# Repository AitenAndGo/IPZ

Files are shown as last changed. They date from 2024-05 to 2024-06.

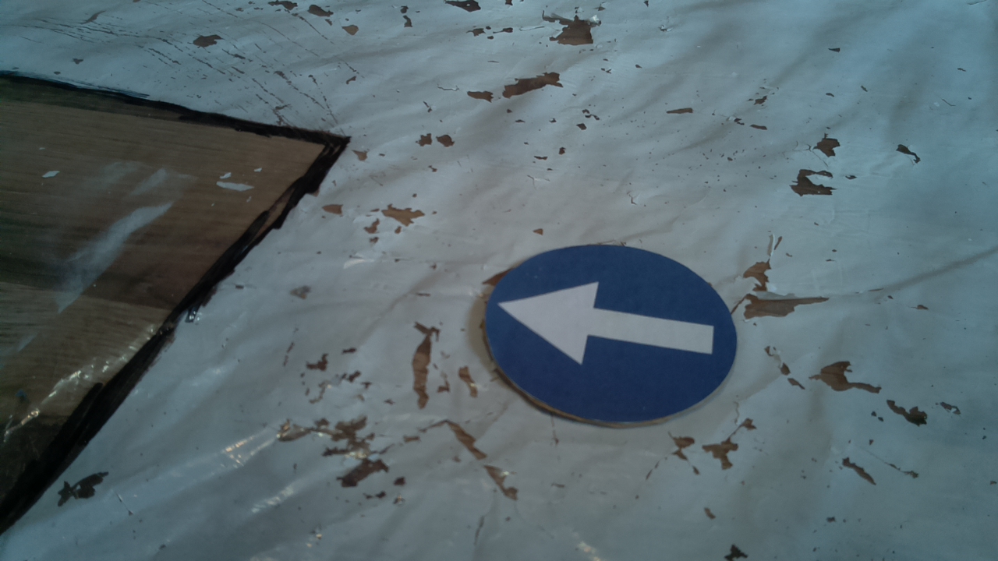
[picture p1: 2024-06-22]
Car/VisionSystem/photos/test/img104.jpg

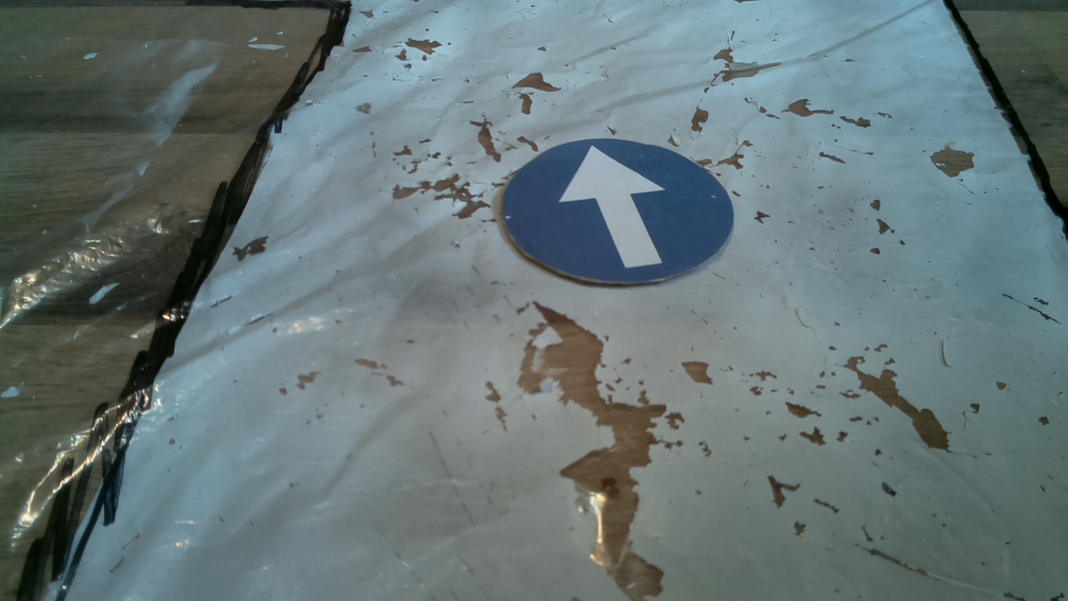
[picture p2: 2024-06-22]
Car/VisionSystem/photos/test/img115.jpg

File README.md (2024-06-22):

# PROJEKT AUTONOMICZENGO SAMOCHODU:
[kliknij aby obejrzeć](url_do_filmu)

# Projekt autonomicznego samochodu 

Celem projektu będzie stworzenie autonomicznego modelu samochodu potrafiącego poruszać się po makiecie miasta ze skrzyżowaniem i światłami, samochód będzie w stanie sam poruszać się po drodze, odpowiednio reagować na światła drogowe, oraz podejmować decyzje o swojej trasie.

___
## 1. Wprowadzenie
W ramach kursu *Interdyscyplinarny projekt zespołowy* przez 15 tygodni w grupie 4 osób będziemy pracować nad stworzeniem automocznego pojazdu, potrafiącego poruszać się na stworzonej drodze i reagować na światła drogowe. Cały projekt jest udokumentowany a pliki będą dostępne [tutaj](https://github.com/AitenAndGo/IPZ "tutaj!"). Rownież poniżej będzie dostępny i pokazany cały proces tworzenia projektu, więc chętne osoby będą mogły spróbować odtworzyć tą koncepcję. Samo stowrzenie takiego pojazdu wraz z całym systemem i makietą jest zadaniem wymagającym dużej wiedzy z zakresu programowania, elektroniki i mechaniki. Do dzieła!

## 2. Cele projektu
+ zbudowanie pojazdu mobilnego
+ stworzenie środowiska po którym będzie poruszał się pojazd
+ stowrzenie systemu świateł drogowych na skrzyżowaniu
+ implementacja oprogramowania z systemem wizyjnym
+ stworzenie bazy danych
+ stworzenie strony internetowej

## 3. Plan projektu
Szczegółowy plan projektu dostępny jest [tutaj](https://github.com/AitenAndGo/IPZ/blob/main/Documentation/Plan.txt "tutaj!")

___
# Realizacja
Realizacja projektu skłądała się na 4 główne etapy:
+ Makieta skrzyżowania
+ Strona internetowa
+ Program strujący makietą miasta
+ samochód
Wszystkie potrzebne kody i modele znajdują się na [tutaj](https://github.com/AitenAndGo/IPZ "tutaj!"). Teraz opiszę każdy z etapów, aby przybliżyć sposób w jaki projekt został zrealizowany.
Zaczynajmy!

##  Makieta
Makieta miała składać się ze skrzyżowania, które posiada 4 drogi wejściowe i wszystkie z dróg łączą się ze sobą tworząc zewnętrzy prostokątny pierścień. Na skrzyżowaniu są 4 światła drogowe, każde z nich osobne do kierowania ruchem przy danej drodze wejściowej. przed wjazdem na środek skrzyżowania na każdej z dróg jest również ustawiony czytnik RFID. Czytnik ten za każdym razem, gdy przejeżdza auto ze swoją kartą RFID zczytuje ją i informuje server o tym że dane auto znalazło się właśnie na danej drodze. Aby wszystko mogło działać potrzebny był mikrokontroler do sterowania światłąmi i RFID. Wybraliśmy esp32, które posiada modół bluetooth oraz wifi co ułatwi komunikację z samochodem. Wszystkie światła i czujniki trzebabyło połączyć z mikrokontrolerem co nie jest lada zadaniem. Ze względu na wielkość makiety i ilość potrzebnych połączeń (tutaj warto dodać że czujniki RFID było zkomunikowane za pomocą protokołu SPI), wykorzystaliśmy płytkę prototypową do dzięki której uzyskaliśmy uporządkowany i zchludny układ elektryczny makiety.
Poniżej pewne zdjęcia i filmy przedstawiające proces powstawania makiety:
makieta
435650640_2062892654094104_2510210449119449921_n
440818486_815108286667908_91705931173108030_n


## Program sterujący makietą
Makieta zwana przez nas "miastem" pełni w tym projekcie wiele aspektów. Odpowiada ona za odpowiednie przełączanie świateł, komunikuje się z serverem i przesyła informacje o odczytanych przejazdach samochodu, oraz musi komunikować się z samochodem aby informować go w momencie gdy przejeżdża on przez skrzyżowanie czy aktualne światło mu na to zezwala. Wszelkie kody można znaleźć w katalogu projektu i powinny one wyjaśnić wszelkie niepewności.

## Strona internetowa
Projekt miał być tak zrobiony, że w teorii można by było wiele samochodów puścić po podobnej makiecie, tylko większej. W związku z tym na serwerze python-anywhere postawiono bardzo prostą stronę internetową (Flask + HTML) oraz podłączono do niej relacyjną bazę danych (MySQL). Baza ta ma 3 tabele: Car, Server oraz City_Trafic. W pierwszej tabeli są wszystkie samochody, które mogą jeździć po makiecie - każdy ma swoje ID oraz status isDriving (czy aktualnie ejst w trakcie jazdy). Dodatkowo przy każdy są przyciski START i STOP - samochody maja być autonomiczne i można nimi sterowac z poziomu strony internetowej, klikając w przycisk Start samochód o danym ID startuje. Druga tabela Server przechowuje informacje o tym, o której godzinie zaczął i skończył jazdę samochód o danym ID w mieście o danym ID. Trzecia tabela to jest kontrola, o której godzinie samochód o danym ID przejechał przez światła (w naszym projekcie były 4: Północ, Południe, Wschód i Zachód).





## Samochód
Na samochód składają się w sumie 4 części:
+ model 3D
+ elektronika
+ model do rozpoznawania znaków
+ program sterujący
Pliki .stl do wydrukowania modelu samochodu można znaleźć w repozytrium projektu. Składa się z dwóch warst, pomiędze znajduje się powerbank, który głównie determinuje wymiary samochodu. Zawera specjalny uchwyt na kamerę a sterowanie kołami przednimi odbywa się przy pomocy micro-serva. W kontekście elektroniki samochód jest napędzany dwoma silnikami na tylnej osi. Silniki są kontrolowane sygnałąmi PWM z drivera LN289. Zasilanie silników jest z pakietu Li-Po 3s i przetwornicy zmniejszającej napięcie do 6V. Głównym komponentem jest RaspberryPi 4 które pełni funkcję sterowania całym samochodem. Złożony samohchód wygląda następująco:

Do rozpoznawania znaków użyto biblioteki fastAi, która kożysta z PyTorch. Zostało zrobione łącznie 400 zdjęć o 4 różnych etykietach tj. prawo, lewo, prosto i bez znaku. Następnie wytrenowano model zgodnie z kodem dostępnym w repozytorium projektu. Całość została wykonany w google colab więc w łatwy sposób można prześledzić tok postępowania. Gotowy model posiadał błąd w wysokości 1%.
Najtrudniejszym zadaniem było stworzenie programu do sterowania. Aby przygotować program jeszcze przed stworzeniem samochodu i dostępem do mikrokomputera została stworzona symulacja w środowisu Unity. Symulacja pozwalała na przygotowanie podstaw skryptu. Działanie skryptu i symulacji przedstawia poniższe nagranie:
### SIMULATION VIDEO:
[kliknij aby obejrzeć](https://github.com/AitenAndGo/IPZ/assets/87769038/a0adc0f1-8832-4500-9a60-e44e0641514c "tutaj!")

Następnie gdy samochód był gotowy należało przygotować środowisko na raspberry. W celu instalacji wszystkich bibliotek zaleca się skorzystanie z minicondy i następnie na stworzonym wirtualnym środowisku zainstalować wszystkie wszystkie biblioteki. Ważne jest również aby system był odpowiedi do zainstalowania PyTorch (potrzebny system 64-bitowy). Program składa się z lokalnej strony na której można mieć podgląd na żywo z widoku kamery co jest bardzo pomocne do debugowania błędów. 
### REMOTLY CONTROLLED CAMERA TEST

[kliknij aby obejrzeć](https://github.com/AitenAndGo/IPZ/assets/87769038/37e9659a-60ab-4ea5-bf75-93e4743b6fed "tutaj!")

Gdy wszystko było przygotowane możnabyło przetestować kod na stowrzonym testowtm torze. Po wielu próbach osiągnięto pozytywne rezultaly co prezentuje poniższy film:

[kliknij aby obejrzeć](https://github.com/AitenAndGo/IPZ/assets/87769038/8e6763ad-770e-4cb4-8f08-51653d83972e "tutaj!")

Całość już połączonego systmu wszytskich elementó można zobaczyć na głównym filmie przedstawiającym cały projekt!.

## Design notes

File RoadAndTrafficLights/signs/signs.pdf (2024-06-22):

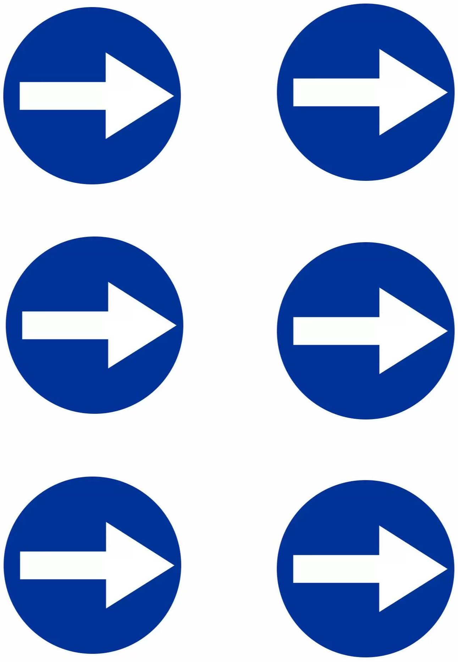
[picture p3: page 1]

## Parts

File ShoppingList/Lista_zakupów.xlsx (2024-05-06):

Nazwa: | Ilość: | Cena/1szt.: | Cena całkowita: | Link:
silnik z kołem (mamy 2, potrzebujemy 2) | 4 | 7 | 28 | https://botland.com.pl/silniki-dc-katowe-z-przekladnia/3696-kolo-silnik-65x26mm-5v-z-przekladnia-48-1-5903351248129.html
Serwo do kół przednich | 1 | 23 | 23 | https://botland.com.pl/serwa-typu-micro/20435-serwo-mg-90s-micro-180-stopni-metalowa-przekladnia-5904422380915.html
Driver do silników | 1 | 19 | 19 | https://botland.com.pl/arduino-shield-kontrolery-silnikow-i-serw/8224-l293d-motor-driver-board-sterownik-silnikow-16v06a-nakladka-dla-arduino-iduino-st1138-59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
goldpin | 1 | 10 | 10 | https://botland.com.pl/gniazda-szpilkowe-goldpin/9499-zestaw-zlacz-dla-esp32-thing-2x-1x20-raster-254mm-sparkfun-prt-14311-5904422313494.html
Płytka drukowana | 1 | 10 | 10 | https://botland.com.pl/plytki-uniwersalne/20269-plytka-drukowana-uniwersalna-dwustronna-90x150mm-5904422380533.html
Czujniki RfiD | 4 | 15 | 60 | https://botland.com.pl/moduly-i-tagi-rfid/6765-modul-rfid-mf-rc522-1356mhz-spi-karta-i-brelok-5904422335014.html
bateria lipo do silników | 1 | 36 | 36 | https://botland.com.pl/akumulatory-li-pol-3s-111v-/1307-pakiet-li-pol-redox-700mah-20c-3s-111v-5903754000454.html
ESP | 1 | 50 | 50 | https://botland.com.pl/moduly-wifi-i-bt-esp32/8893-esp32-wifi-bt-42-platforma-z-modulem-esp-wroom-32-zgodny-z-esp32-devkit-5904422337438.html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
śrubki i nakrętki (zestaw) | 1 | 11.9 | 11.9 | https://botland.com.pl/srubki-i-nakretki/637-zestaw-srubek-podkladek-i-nakretek-330szt-5410329304478.html
 |  |  | 247.9

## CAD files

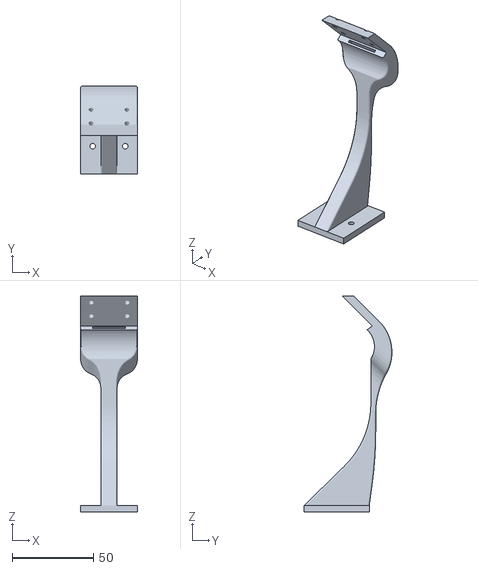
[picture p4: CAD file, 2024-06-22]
Car/mechanics/car/stlFiles/kamera_uchwyt_3.stl
35.0 x 53.9 x 132.5

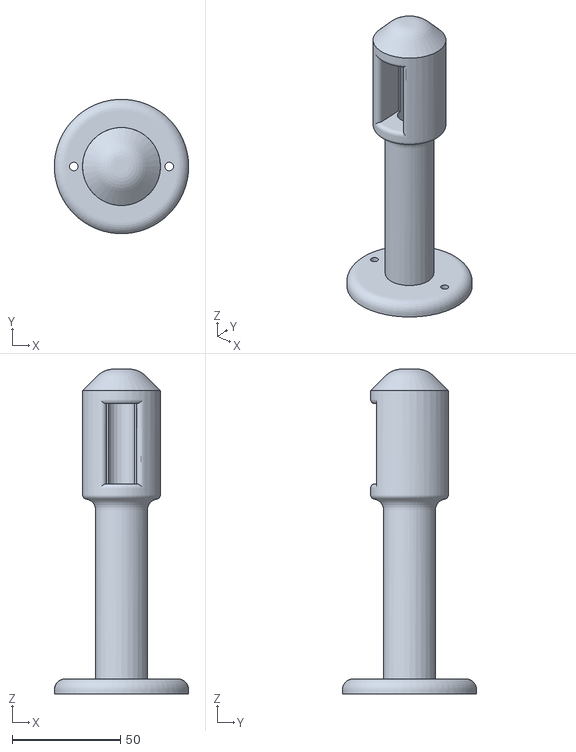
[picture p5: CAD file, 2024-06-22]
RoadAndTrafficLights/models/swiatla.stl
62.0 x 62.0 x 150.0

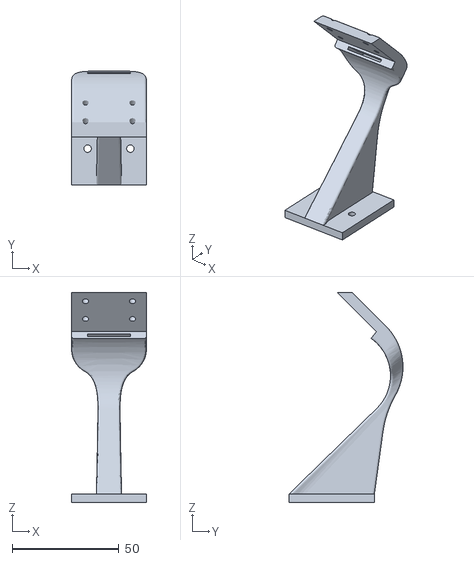
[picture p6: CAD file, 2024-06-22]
Car/mechanics/car/stlFiles/kamera_uchwyt_2.stl
35.0 x 53.4 x 98.4

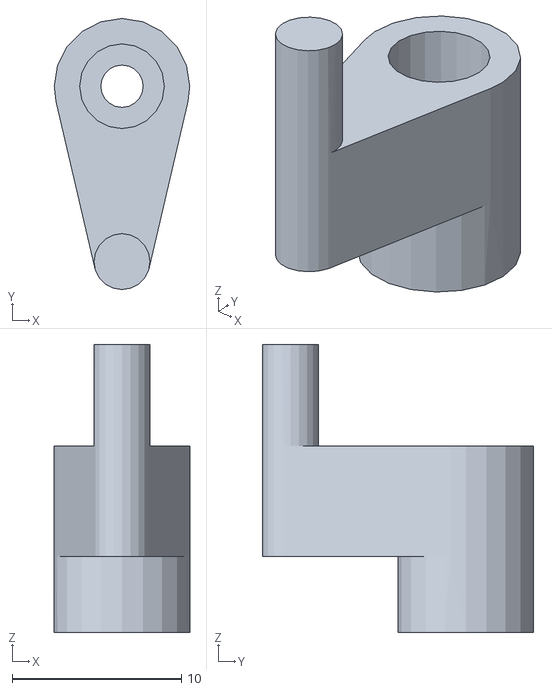
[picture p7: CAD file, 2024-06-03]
Car/mechanics/car/stlFiles/ServoSteereingThing.stl
8.00 x 16.0 x 17.0

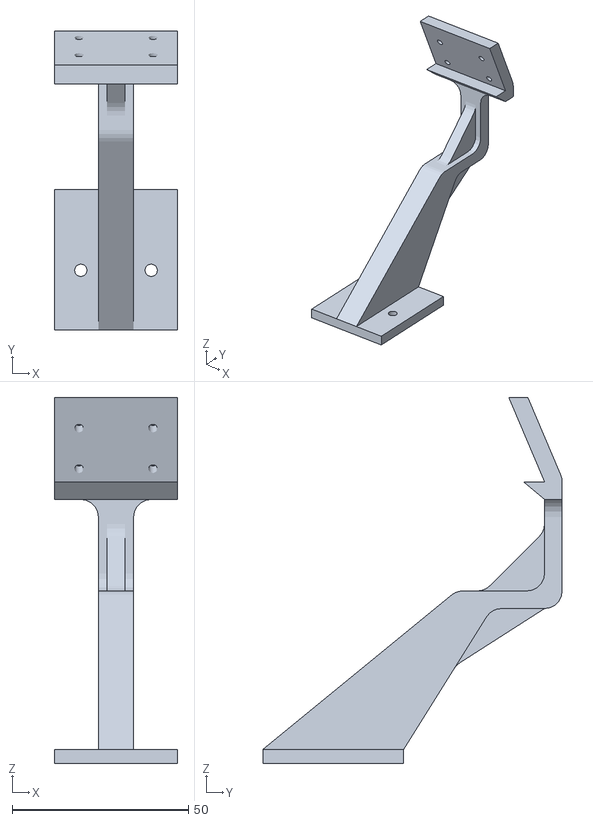
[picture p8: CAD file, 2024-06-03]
Car/mechanics/car/stlFiles/kamera_uchwyt_1.stl
35.0 x 85.0 x 103.9

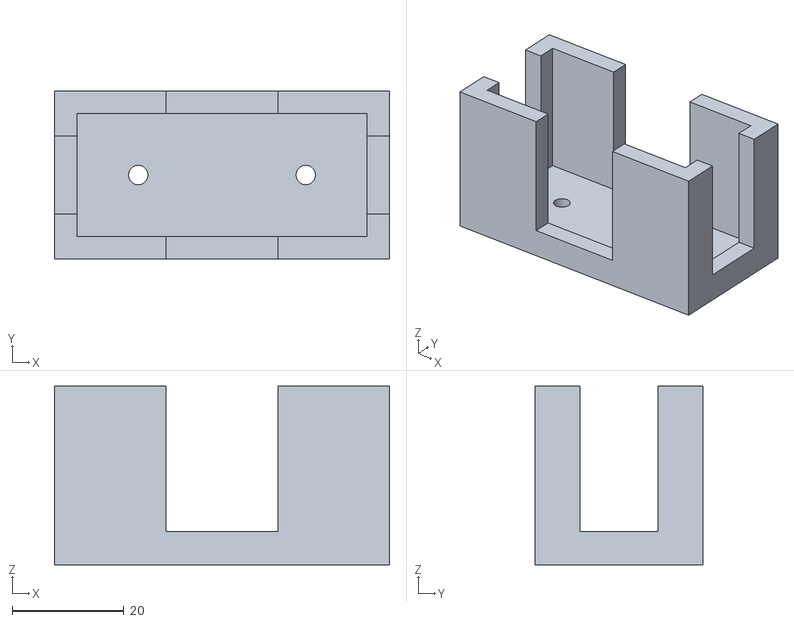
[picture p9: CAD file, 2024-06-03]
Car/mechanics/car/stlFiles/koszyk_na_lipo_2.stl
60.0 x 30.0 x 32.0

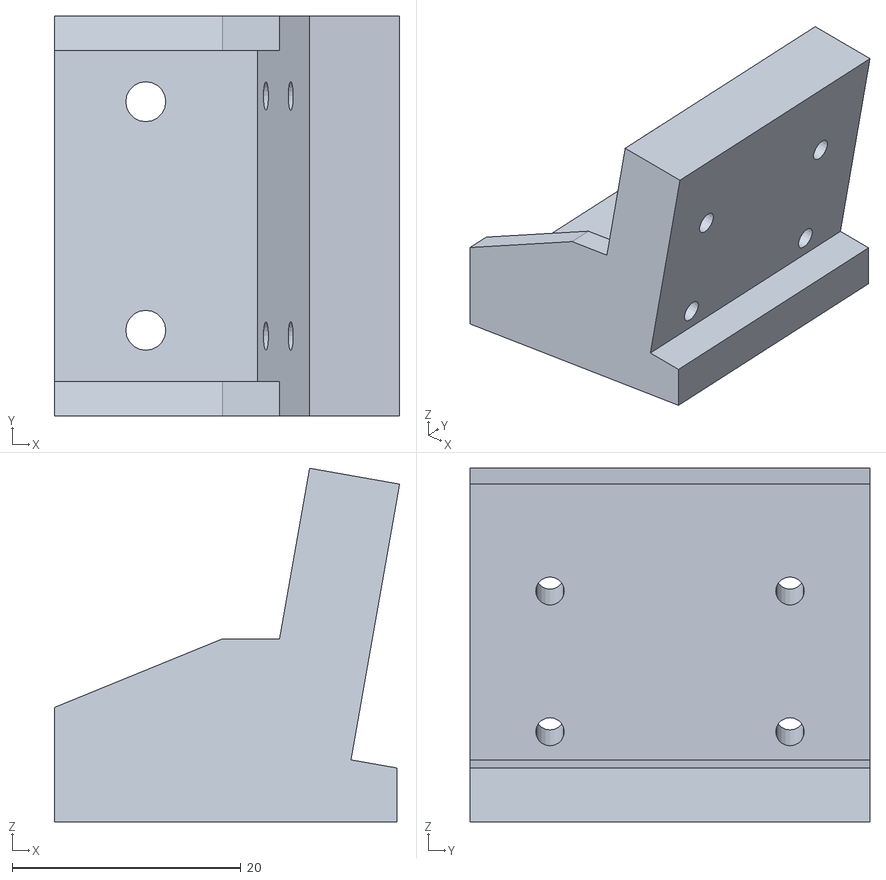
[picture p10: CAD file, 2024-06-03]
Car/mechanics/car/stlFiles/uchwyt_na_kamere_1_1.stl
30.2 x 35.0 x 30.9

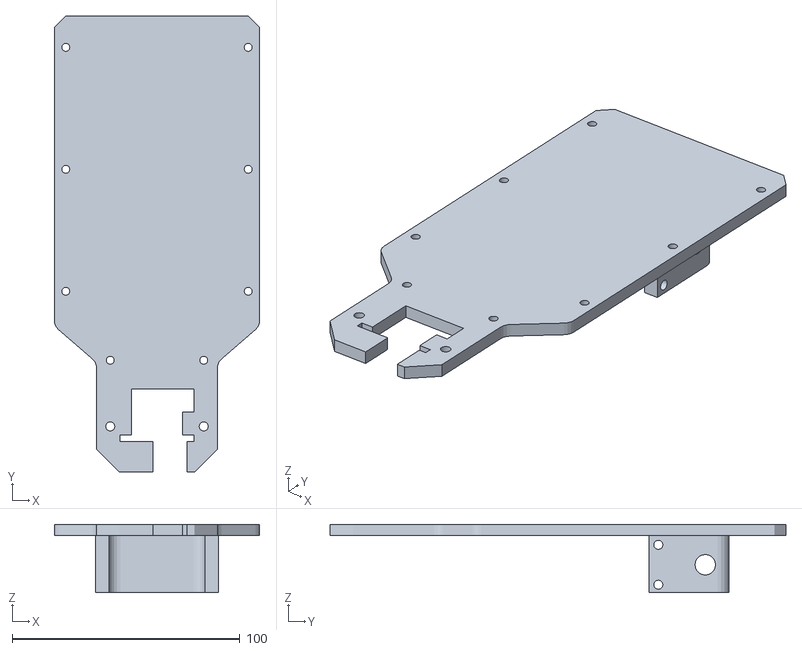
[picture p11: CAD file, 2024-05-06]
Car/mechanics/car/stlFiles/podwozie.stl
90.0 x 200.0 x 30.0

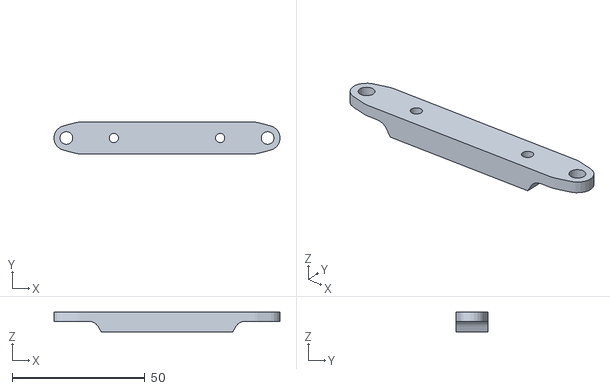
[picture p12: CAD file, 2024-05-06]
Car/mechanics/car/stlFiles/belka.stl
85.1 x 12.0 x 7.50

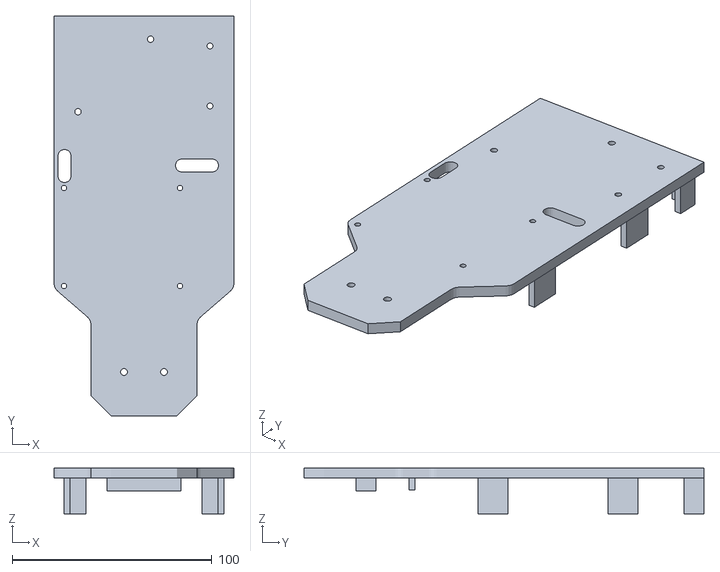
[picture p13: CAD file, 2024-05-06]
Car/mechanics/car/stlFiles/drugaWarstwa.stl
90.0 x 200.0 x 23.0

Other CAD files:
Car/mechanics/car/stlFiles/kamera_uchwyt.stl
Car/mechanics/car/stlFiles/podwozie_1.stl
Car/mechanics/car/First_idea/Modelauta.prt
Car/mechanics/car/First_idea/drugaWarstwa.prt
Car/mechanics/car/First_idea/kolek.prt
Car/mechanics/car/First_idea/kolo.prt
Car/mechanics/car/First_idea/mostekH.prt
Car/mechanics/car/First_idea/powerbank.prt
Car/mechanics/car/First_idea/samochodzik.prt
Car/mechanics/car/First_idea/silnik.prt
Car/mechanics/car/Second_idea/aucisko.prt
Car/mechanics/car/Second_idea/drugaWarstwa1.prt
Car/mechanics/car/Second_idea/kolek1.prt
Car/mechanics/car/Second_idea/kolo1.prt
Car/mechanics/car/Second_idea/lacznik.prt
Car/mechanics/car/Second_idea/nowy_rama1.prt
Car/mechanics/car/Second_idea/oska.prt
Car/mechanics/car/Second_idea/powerbank1.prt
Car/mechanics/car/Second_idea/rasberry.prt
Car/mechanics/car/Second_idea/serwo.prt
Car/mechanics/car/Second_idea/silnik.prt
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

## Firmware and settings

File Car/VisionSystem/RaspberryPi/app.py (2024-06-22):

from flask import Flask, render_template, Response
import threading
import cv2
from time import sleep
import RPi.GPIO as GPIO
import numpy as np
import serial
import requests
# from fastai.vision.all import load_learner, PILImage  # for sign recognition

uuid = "malinka"

# GPIO

FORWARD_RIGHT = 16
FORWARD_LEFT = 18
BACKWARD_RIGHT = 11
BACKWARD_LEFT = 13

Motor1Enable_PIN = 32
Motor2Enable_PIN = 33

SERVO_PIN = 12


# Defines

MAX_ANGLE = 60
MAX_LEFT = 150
MAX_RIGHT = 30


# Setup

GPIO.setmode(GPIO.BOARD)

GPIO.setup(FORWARD_RIGHT,   GPIO.OUT)
GPIO.setup(BACKWARD_RIGHT,  GPIO.OUT)
GPIO.setup(FORWARD_LEFT,    GPIO.OUT)
GPIO.setup(BACKWARD_LEFT,   GPIO.OUT)

GPIO.setup(Motor1Enable_PIN,GPIO.OUT)
GPIO.setup(Motor2Enable_PIN,GPIO.OUT)
MOTOR_1 = GPIO.PWM(Motor1Enable_PIN, 1000)
MOTOR_2 = GPIO.PWM(Motor2Enable_PIN, 1000)

MOTOR_1.start(0)
MOTOR_2.start(0)

GPIO.setup(SERVO_PIN,       GPIO.OUT)
SERVO = GPIO.PWM(SERVO_PIN, 50)
SERVO.start(0)

app = Flask(__name__)

camera = cv2.VideoCapture(0)  # Use the PiCamera


# Get camera dimensions
width = int(camera.get(cv2.CAP_PROP_FRAME_WIDTH))
height = int(camera.get(cv2.CAP_PROP_FRAME_HEIGHT))

detectionWindow = np.zeros((height, width), dtype='uint8')

leftBottom = (int(0.01 * width), int(0.8 * height))
rightBottom = (int((1 - 0.01) * width), int(0.8 * height))
leftTop = (int(0.01 * width), int(0.3 * height))
rightTop = (int((1 - 0.01) * width), int(0.3 * height))

vertices = [leftBottom, rightBottom, rightTop, leftTop]
vertices = np.array([vertices], dtype=np.int32)

cv2.fillConvexPoly(detectionWindow, vertices, 255)

# crossroad

# right turn check polygon
leftTurnWindow = np.zeros((height, width), dtype='uint8')

leftBottom = (int(0), int(0.1 * height))
rightBottom = (int((0.1) * width), int(0.1 * height))
leftTop = (int(0), int(0.0 * height))
rightTop = (int((0.1) * width), int(0.0 * height))
vertices = [leftBottom, rightBottom, rightTop, leftTop]
vertices = np.array([vertices], dtype=np.int32)
cv2.fillConvexPoly(leftTurnWindow, vertices, 255)
leftPixels = len(np.argwhere(leftTurnWindow > 0))

# left turn check polygon
rightTurnWindow = np.zeros((height, width), dtype='uint8')

leftBottom = (int(width), int(0.1 * height))
rightBottom = (int((0.9) * width), int(0.1 * height))
leftTop = (int(width), int(0.0 * height))
rightTop = (int((0.9) * width), int(0.0 * height))
vertices = [leftBottom, rightBottom, rightTop, leftTop]
vertices = np.array([vertices], dtype=np.int32)
cv2.fillConvexPoly(rightTurnWindow, vertices, 255)
rightPixels = len(np.argwhere(rightTurnWindow > 0))

# go forward check polygon
forwardWindow = np.zeros((height, width), dtype='uint8')

leftBottom = (int(0.2 * width), int(0.15 * height))
rightBottom = (int((0.8) * width), int(0.15 * height))
leftTop = (int(0.2 * width), int(0.25 * height))
rightTop = (int((0.8) * width), int(0.25 * height))
vertices = [leftBottom, rightBottom, rightTop, leftTop]
vertices = np.array([vertices], dtype=np.int32)
cv2.fillConvexPoly(forwardWindow, vertices, 255)
forwardPixels = len(np.argwhere(forwardWindow > 0))


WebImage = np.zeros((int(height), int(width)))


def move_forward(speed):
    MOTOR_1.ChangeDutyCycle(speed)
    MOTOR_2.ChangeDutyCycle(speed)
    GPIO.output(BACKWARD_RIGHT, GPIO.LOW)
    GPIO.output(BACKWARD_LEFT,  GPIO.LOW)
    GPIO.output(FORWARD_RIGHT,  GPIO.HIGH)
    GPIO.output(FORWARD_LEFT,   GPIO.HIGH)

def move_backward(speed):
    MOTOR_1.ChangeDutyCycle(speed)
    MOTOR_2.ChangeDutyCycle(speed)
    GPIO.output(FORWARD_RIGHT,  GPIO.LOW)
    GPIO.output(FORWARD_LEFT,   GPIO.LOW)
    GPIO.output(BACKWARD_RIGHT, GPIO.HIGH)
    GPIO.output(BACKWARD_LEFT,  GPIO.HIGH)



def stop():
    GPIO.output(BACKWARD_RIGHT, GPIO.LOW)
    GPIO.output(BACKWARD_LEFT,  GPIO.LOW)
    GPIO.output(FORWARD_RIGHT,  GPIO.LOW)
    GPIO.output(FORWARD_LEFT,   GPIO.LOW)

def turn(angle):

    if angle < (90 - MAX_ANGLE):
        angle = 90 - MAX_ANGLE
    elif angle > (90 + MAX_ANGLE):
        angle = 90 + MAX_ANGLE


    duty_cycle = 2 + (angle / 18)
    SERVO.ChangeDutyCycle(duty_cycle)
    sleep(0.1)
    SERVO.ChangeDutyCycle(0)

def turnCar(dir):
    turn(80 + (dir))

def perspective2TopDown(frame):
    perspectivePoints = np.float32([[185,310],[483,306],[233,172],[434,172]])
    for pt in perspectivePoints:
        cv2.circle(frame, tuple(pt.astype(np.int32)), 3, (0,0,255), -1)

    topDownPoints = np.float32([[450,650],[650,650],[450,450],[650,450]])
    M = cv2.getPerspectiveTransform(perspectivePoints,topDownPoints)
    dst = cv2.warpPerspective(frame,M,(1080,720))
    return dst

def calculateDirection(img):
    leftHalf = img[:, :img.shape[1]//2]
    righttHalf = img[:, img.shape[1]//2:]
    Lpoints = np.argwhere(leftHalf > 0)
    Rpoints = np.argwhere(righttHalf > 0)
    dir = (len(Lpoints) - len (Rpoints)) / 1000
    # print(dir)
    return dir

def process_frame(frame):
    
    # frame = cv2.flip(frame, 1)
    # frame = cv2.flip(frame, 0)
    
    image_original = frame
    
    # frame = perspective2TopDown(frame)
    frame = cv2.cvtColor(frame, cv2.COLOR_BGR2GRAY)
    blur = cv2.GaussianBlur(frame, (11, 11), 3)
    ret, frame = cv2.threshold(frame, 30, 255, cv2.THRESH_BINARY_INV)
    # frame = cv2.adaptiveThreshold(frame,255,cv2.ADAPTIVE_THRESH_GAUSSIAN_C,\
    #  cv2.THRESH_BINARY_INV,11,2)
    ret, otsu = cv2.threshold(blur, 0, 255, cv2.THRESH_BINARY + cv2.THRESH_OTSU)
    # frame = cv2.bitwise_and(frame, detectionWindow)

    # frame = cv2.Laplacian(frame,cv2.CV_64F)
    # kernel = np.ones((5, 5), np.uint8)
    # mask_road = cv2.morphologyEx(frame, cv2.MORPH_CLOSE, kernel)
    # mask_road = cv2.morphologyEx(frame, cv2.MORPH_OPEN, kernel)
    # edges = cv2.dilate(frame,kernel,iterations = 1)
    # lines = cv2.HoughLinesP(edges,1,np.pi/180,100,minLineLength=100,maxLineGap=10)

    # blank = np.zeros_like(frame)
    # if lines is not None:
    #     for line in lines:
    #         x1, y1, x2, y2 = line[0]
    #         cv2.line(image_original, (x1, y1), (x2, y2), (0, 255, 0), 10)
    
    
    otsu = cv2.bitwise_not(otsu)
    return frame

def nextTurn(img, left, right, lpix, rpix):
    ra = cv2.bitwise_and(img, right)
    la = cv2.bitwise_and(img, left)

    rp = len(np.argwhere(ra > 0)) / rpix
    lp = len(np.argwhere(la > 0)) / lpix

    turn = []
    if rp > 0.97:
        return "R"
    elif lp > 0.97:
        return "L"
    else:
        return None 

def endOfRoad(img, forward, fpix):
    fa = cv2.bitwise_and(img, forward)
    fp = len(np.argwhere(fa > 0)) / fpix

    if fp < 0.05:
        return True
    else:
        return False

def hardTurn(direction):
    if direction == "R":
        turn(80 + (MAX_RIGHT))
    elif direction == "L":
        turn(80 + (MAX_LEFT))
    
    
def gen_frames():
    while True:
        succes, frame = camera.read()
        if not succes:
            pass
        else:
            # frame = process_frame(frame)
            ret, buffer = cv2.imencode('.jpg', frame)
            frame = buffer.tobytes()
            yield (b'--frame\r\n'
                   b'Content-Type: image/jpeg\r\n\r\n' + frame + b'\r\n')
@app.route('/')
def index():
    return render_template('index.html')

@app.route('/video_feed')
def video_feed():
    return Response(gen_frames(), mimetype='multipart/x-mixed-replace; boundary=frame')

def webCamera():
    app.run(host='0.0.0.0', port=5000)

def cv2_to_pil(img):
    img_rgb = cv2.cvtColor(img, cv2.COLOR_BGR2RGB)
    pil_img = PILImage.create(img_rgb)
    return pil_img

def startCar():
    url = "https://miszczak13.eu.pythonanywhere.com/postCar"
    data = {"uuid": uuid}
    headers = {"Content-Type": "application/json"}
    
    try:
        response = requests.post(url, json=data, headers=headers)
        response.raise_for_status()
    
        if response.headers.get('Content-Type') == 'application/json':
            print(response.json())
        else:
            print("Odpowiedź nie jest w formacie JSON:", response.text)
    
    except requests.exceptions.HTTPError as errh:
        print(f"HTTP Error: {errh}")
    except requests.exceptions.ConnectionError as errc:
        print(f"Error Connecting: {errc}")
    except requests.exceptions.Timeout as errt:
        print(f"Timeout Error: {errt}")
    except requests.exceptions.RequestException as err:
        print(f"Something went wrong: {err}")

def getStatus():

    url = f'https://miszczak13.eu.pythonanywhere.com/get_car_status?uuid={uuid}'
    try:
        response = requests.get(url)
        response.raise_for_status()  # Rzuć wyjątek w przypadku błędu HTTP

        try:
            car_status = response.json()  # Spróbuj zdekodować odpowiedź jako JSON
            print(f"UUID: {car_status['uuid']}, isDriving: {car_status['isDriving']}")
        except ValueError:
            print("Niepoprawny format JSON w odpowiedzi")
        except KeyError as e:
            print(f"Brak oczekiwanego klucza 'uuid' lub 'isDriving' w odpowiedzi: {e}")

    except requests.exceptions.RequestException as e:
        print(f"Wystąpił błąd podczas żądania: {e}")

if __name__ == '__main__':
    webCamera() # visualization
    startCar()
    # ser = serial.Serial('/dev/rfcomm0', 115200) # for bluetooth with city lights
    # learn = load_learner('model.pkl')
    Turn = "R"
    try:
        move_forward(75)
        while True:
            status = getStatus()
            # if ser.in_waiting > 0:
                # data = ser.read(ser.in_waiting).decode() #BLUETOOTH
            if status:    
                print("go!")
                move_forward(75)
                succes, frame = camera.read()
                if not succes:
                    pass;
                else:
                    # pil_frame = cv2_to_pil(frame)
                    # # Wykonaj predykcję na ramce
                    # pred, pred_idx, probs = learn.predict(pil_frame)
                    # print(pred)
                    frame = process_frame(frame)
                    _turn = nextTurn(frame, leftTurnWindow, rightTurnWindow, leftPixels, rightPixels)
                    if _turn is not None:
                        Turn = _turn
                    if endOfRoad(frame, forwardWindow, forwardPixels):
                        hardTurn(Turn)
                        print("TURN" + Turn)
                        sleep(1)
                    else:
                        dir = calculateDirection(frame)
                        # print(dir)
                        turnCar(dir)
            else:
                stop()
                print('stop')
                # angle = input("Enter angle (0-180): ")
                # if angle == 'w':
                    # move_forward(90)
                # elif angle == 's':
                    # move_backward(90)
                # elif angle == 'x':
                    # stop()
                # else:
                    # turn(float(angle))
                # move_forward(90)
    except KeyboardInterrupt:
        pass
    finally:
        SERVO.stop()
        GPIO.cleanup()

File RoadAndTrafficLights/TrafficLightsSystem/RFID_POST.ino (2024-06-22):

#include <SPI.h>
#include <MFRC522.h>
#include <WiFi.h>
#include <ArduinoJson.h>
#include <HTTPClient.h>
#include <WiFiMulti.h>
#include <TimeLib.h>

#define SS_PIN_1 21
#define SS_PIN_2 2
#define SS_PIN_3 16
#define SS_PIN_4 5

#define RST_PIN_1 4
#define RST_PIN_2 15
#define RST_PIN_3 14
#define RST_PIN_4 2

MFRC522 rfid_1(SS_PIN_1, RST_PIN_1); // Instance of the class
MFRC522 rfid_2(SS_PIN_2, RST_PIN_2);
MFRC522 rfid_3(SS_PIN_3, RST_PIN_3); // Corrected RST_PIN for this instance
MFRC522 rfid_4(SS_PIN_4, RST_PIN_4);
WiFiMulti wifiMulti;
//connecting to WiFi w domu
/**/
const char* ssid = "HH71V1_3A49_2.4G";
const char* password = "pYRyNYde";

MFRC522::MIFARE_Key key; 

// Init arrays to store new NUID for each RFID reader
byte nuidPICC_1[4];
byte nuidPICC_2[4];
byte nuidPICC_3[4];
byte nuidPICC_4[4];

void setup() { 
  Serial.begin(9600);
  SPI.begin(); // Init SPI bus

  rfid_1.PCD_Init(); // Init MFRC522 
  rfid_2.PCD_Init();
  rfid_3.PCD_Init(); // Init MFRC522 
  rfid_4.PCD_Init();

  for (byte i = 0; i < 6; i++) {
    key.keyByte[i] = 0xFF;
  }

  Serial.println(F("This code scans the MIFARE Classic NUID."));
  Serial.print(F("Using the following key:"));
  printHex(key.keyByte, MFRC522::MF_KEY_SIZE);
  wifiMulti.addAP(ssid, password);
}

String byteToHex(byte *buffer, byte bufferSize)
 {
  String hexString = "";
  char tmp[3];
  for (byte i = 0; i < bufferSize; i++) {
  sprintf(tmp, "%02X", buffer[i]);
  hexString += String(tmp);
  }
  return hexString;
}


void readRFID(MFRC522& rfid, byte* nuidPICC, int ss_pin) {
  // Activate the RFID module
  digitalWrite(ss_pin, LOW);
  String nuid;
  // Reset the loop if no new card present on the sensor/reader. This saves the entire process when idle.
  if (rfid.PICC_IsNewCardPresent()) {
    // Verify if the NUID has been read
    if (rfid.PICC_ReadCardSerial()) {
      Serial.print(F("PICC type: "));
      MFRC522::PICC_Type piccType = rfid.PICC_GetType(rfid.uid.sak);
      Serial.println(rfid.PICC_GetTypeName(piccType));

      // Check if the PICC is of Classic MIFARE type
      if (piccType == MFRC522::PICC_TYPE_MIFARE_MINI || 
          piccType == MFRC522::PICC_TYPE_MIFARE_1K ||
          piccType == MFRC522::PICC_TYPE_MIFARE_4K) {

          Serial.println(F("A new card has been detected."));

          // Store NUID into nuidPICC array
          for (byte i = 0; i < 4; i++) {
            nuidPICC[i] = rfid.uid.uidByte[i];
          }

          Serial.println(F("The NUID tag is:"));
          Serial.print(F("In hex: "));
          printHex(rfid.uid.uidByte, rfid.uid.size);
          nuid = byteToHex(rfid.uid.uidByte, rfid.uid.size);
          Serial.println();
          Serial.print(F("In dec: "));
          printDec(rfid.uid.uidByte, rfid.uid.size);
          //Serial.println();
          //Serial.println(nuid);

      } else {
        Serial.println(F("Your tag is not of type MIFARE Classic."));
      }
      String name = "Północ";
      postDataToServer(nuid, name);
      // Halt PICC
      rfid.PICC_HaltA();

      // Stop encryption on PCD
      rfid.PCD_StopCrypto1();
    }
  }

  // Deactivate the RFID module
  digitalWrite(ss_pin, HIGH);
}

void postDataToServer(String dane, String sensor_id) {

Serial.println(F("Posting JSON data to server..."));
// Block until we are able to connect to the WiFi access point
if (wifiMulti.run() == WL_CONNECTED) {
  HTTPClient http;   
  //Serial.println(F("Here1"));
  http.begin("https://miszczak13.eu.pythonanywhere.com/postTrafic");  
  http.addHeader("Content-Type", "application/json");         
  //Serial.println(F("Here2"));
  StaticJsonDocument<200> doc;

  doc["car_id"] = dane;
  doc["timeofstop"] = now();
  doc["sensor_id"] =  sensor_id;

  //Serial.println(F("Here3"));
  String requestBody;
  serializeJson(doc, requestBody);

  Serial.println(requestBody);
  Serial.println(F("Wyslany"));
  
  int httpResponseCode = http.POST(requestBody);

  delay(100);

  if(httpResponseCode>0){
    
    String response = http.getString();                       
    
    Serial.println(httpResponseCode);   
    Serial.println(response);
  }
  else {
    Serial.println(F("Error occurred while sending HTTP POST"));
  }
}
}
bool connected_to_wifi = false;

void loop() {
  readRFID(rfid_1, nuidPICC_1, SS_PIN_1);
  readRFID(rfid_2, nuidPICC_2, SS_PIN_2);
  readRFID(rfid_3, nuidPICC_3, SS_PIN_3);
  readRFID(rfid_4, nuidPICC_4, SS_PIN_4);

  
// wifi connection
WiFi.mode(WIFI_STA); //Optional
WiFi.begin(ssid, password);

while(WiFi.status() != WL_CONNECTED){
  if(!connected_to_wifi){
    Serial.println(F("\nConnecting....."));
    delay(3000);
  }
}

if(!connected_to_wifi)
{
Serial.println(F("\nConnected to the WiFi network"));
Serial.print("Local ESP32 IP: ");
Serial.println(WiFi.localIP());
delay(100);
connected_to_wifi = true;
}
}

/**
 * Helper routine to dump a byte array as hex values to Serial. 
 */
void printHex(byte *buffer, byte bufferSize) {
  for (byte i = 0; i < bufferSize; i++) {
    Serial.print(buffer[i] < 0x10 ? " 0" : " ");
    Serial.print(buffer[i], HEX);
  }
}

/**
 * Helper routine to dump a byte array as dec values to Serial.
 */
void printDec(byte *buffer, byte bufferSize) {
  for (byte i = 0; i < bufferSize; i++) {
    Serial.print(buffer[i] < 0x10 ? " 0" : " ");
    Serial.print(buffer[i], DEC);
  }
}

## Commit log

2024-03-19 added car model
    [Modelauta.prt, drugaWarstwa.prt, kolek.prt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]
2024-03-24 Big update: first intersection working + video + new simulation
    [Modelauta.prt]
2024-03-25 added Shoping List
    [Lista_zakupów.xlsx]
2024-04-08 Update car model
    Added second idea for car model
    [Modelauta.prt, aucisko.prt, drugaWarstwa.prt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]
2024-05-06 New Car Model
    new steering
    [Lista_zakupów.xlsx, Warstwa_2.prt, auto_Assembly.prt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]
2024-05-06 Update Car Model
    Added last concept before assembling parts
    [Auto_as.prt, Modelauta.prt, Warstwa_1.prt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]
2024-06-22 updating files
    [kamera_uchwyt.prt, kamera_uchwyt_2.stl, kamera_uchwyt_3.stl]
2024-06-22 VersionAlpha
    added all files to complite to project
    [swiatla.stl]
